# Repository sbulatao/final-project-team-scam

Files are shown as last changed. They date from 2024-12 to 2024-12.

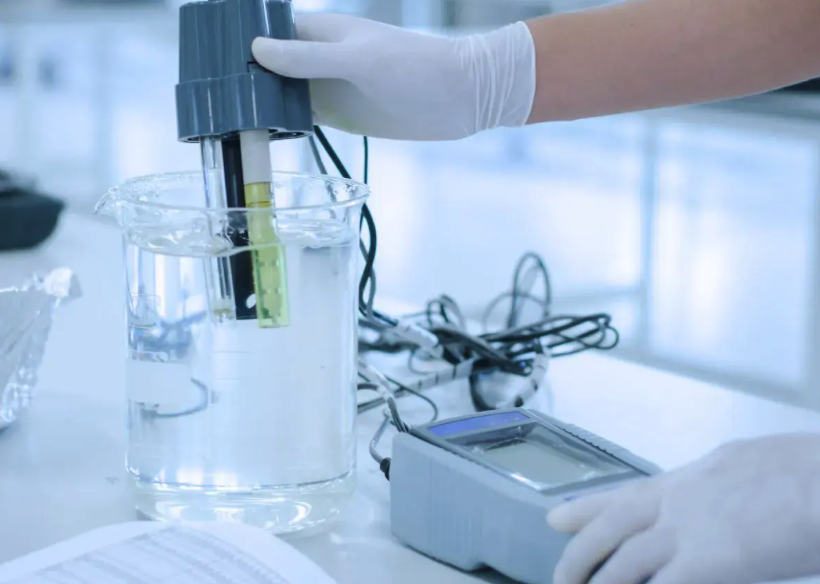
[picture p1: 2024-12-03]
pictures/testingIsh.png

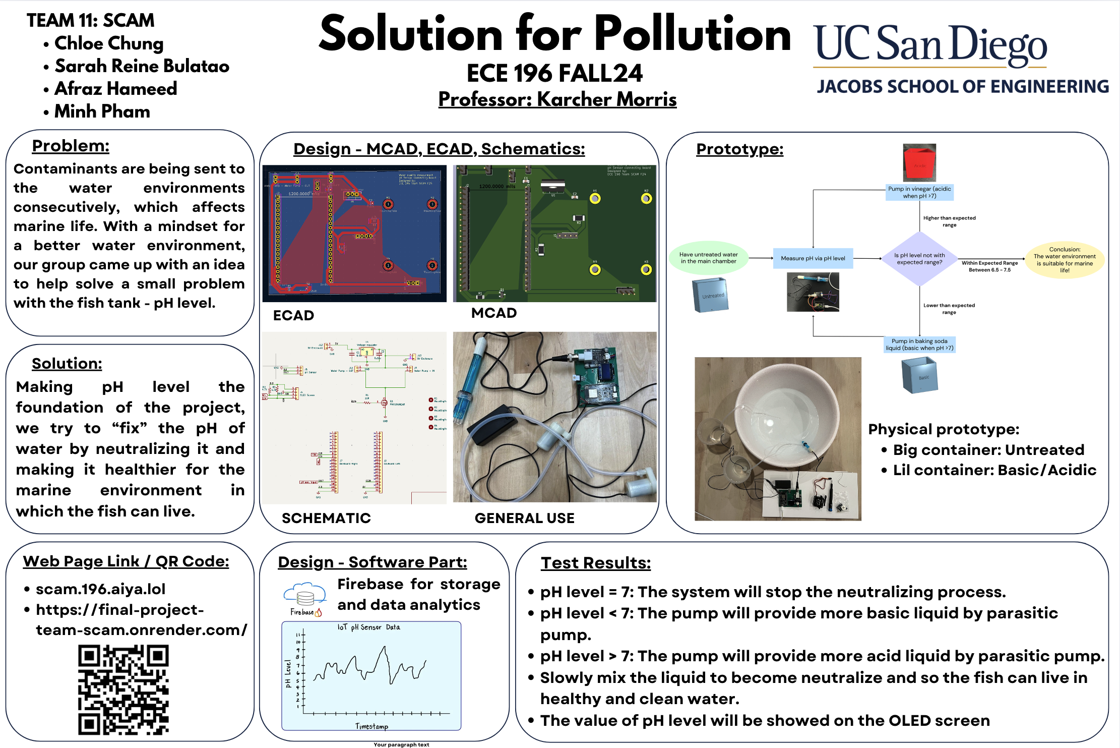
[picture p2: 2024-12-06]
pictures/canvaPoster.png

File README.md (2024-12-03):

# SolutionForpollution
GitHub Repo for ECE 196 Project Managing code, PCB files, 3D design, and more.

## WEBSITES: 
https://scam.196.aiya.lol/

https://final-project-team-scam.onrender.com

## Structure:
- css file contains all the css: the style for the website

- pictures file contains all the pictures: jpeg, png, etc.

- public file contains all the js: the action-ish for the website

- views file contains all the html: the bone structure for the website

## PROBLEM DEFINTION
Stormwater and Sewage Spills contain untreated debris directly into the Tijuana River and Imperial Beach affecting pH of the waters affecting marine life and making it more acidic.

## PROPOSED IDEA
A Real-Time Water pH Regulation Network

 - Big idea is pumping in basic solution in untreated water to regulate pH for marine life
 - Starting with pH sensor to determine levels, and pumping basic solution until it’s a regular level

## TESTABLE HYPOTHESIS
If there is polluted water with a more acidic pH, then our device will read the values and add basic solution until the pH is regular/safe for marine life.

## MILESTONES / TIMELINE
1. Completed PCB design on KiCAD and received parts from shipping
2. Assembled PCB with all necessary SMD’s and components and verified successful communication with computer (the device is recognized)
3. Finished 3D printing for basic solution enclosure, path for tube, body for contaminated water and measurement, and plastic cup to gather and pour water (not 3D printed)
4. Completed code for pH sensor data collection and logging to read and display pH values over time for both regular and contaminated water, with pH data collected and tabulated
5. Finished code and hardware integration for pumping with connections to PCB and recognizing pump in Arduino, basic solution can travel in pump to water and stop pumping when correct pH is read. 
6. Testing and data collection in Untreated Water, testing out conditions for demo by recording video of shown, unclean dirty water with higher pH levels and showing pumping solution regulating pH levels until level is sustainable for marine life.

## References, Citations, Helpful Resources

# HTML References
FreeFrontend. 2016-2024. https://freefrontend.com/css-water-effects/

HTML5UP. https://html5up.net/ (Didn't Use but thinking about it)

## Research / Arduino Build

Fahad, Engr. Electronic Clinic. 8 March 2020. IOT Water Quality Monitoring Using Arduino, pH Sensor, Nodemcu ESP8266. https://www.electroniclinic.com/iot-water-quality-monitoring-using-arduinoph-sensornodemcu-esp8266/

Ani, Emmanuel. hackster.io. 4 May 2024. Water Quality Monitoring and Notification System. https://www.hackster.io/eani/water-quality-monitoring-and-notification-system-f85d23 

YSI: a company that works on the water quality measurement which is The Sydney Institute of Marine Science collaborative
https://www.ysi.com/

United States Environmental Protection Agency. 21 October 2024. Water Quality Standards: Regulations and Resources. https://www.epa.gov/wqs-tech

Standard Methods For the Examination of Water and Wastewater. https://www.standardmethods.org

https://www.nsf.org/nsf-standards/standards-portfolio/water-wastewater-standards

(ERROR 404 GIVEN) https://www.nsf.org/our-services/water-quality

(ERROR 404 GIVEN) https://www.instructables.com/howto/water+quality+monitor/

## Website for the San Diego Coast Keepers EVIDENCE:

- Home page. https://www.sdcoastkeeper.org/
- Stormwater Infrastructure. https://www.sdcoastkeeper.org/water-quality/stormwater-infrastructure-funding/
- Tijuana River Sewage Crisis. https://www.sdcoastkeeper.org/tijuana-river-sewage/

## Other EVIDENCE:

Museg, Phillip. San Diego CoastKeeper. 2 May 2024. Understanding The Tijuana River Sewage Crisis - An Overview of Causes and Consequences. https://www.sdcoastkeeper.org/blog/tijuana-river-sewage-crisis-causes-consequences/

The California Water Boards. 25 September 2024. USIBWC Spill Events and Transboundary Flow Events from Mexico into the San Diego Region. https://www.waterboards.ca.gov/sandiego/water_issues/programs/tijuana_river_valley_strategy/sewage_issue.html

SDSU News Team. 14 February 2024. New Report: Public Health Crisis Unfolds as Tijuana River Sewage Contamination Escalates. https://www.sdsu.edu/news/2024/02/public-health-crisis-unfolds-as-tijuana-river-sewage-contamination-escalates

Shin, Tony. Fox 5 Kusi News. 11 September 2024. Imperial Beach Sewage Crisis Causing Fears of Long-Term Illnesses. https://fox5sandiego.com/news/local-news/imperial-beach-sewage-crisis-causing-fears-of-long-term-illnesses/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,closed%20for%20over%201%2C000%20days.

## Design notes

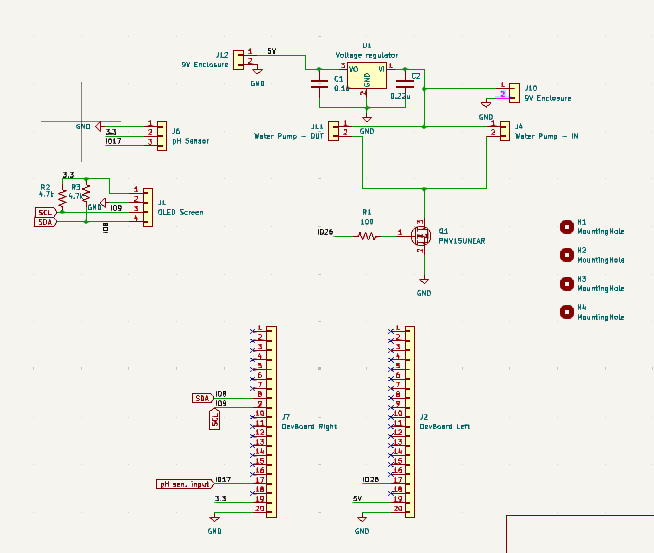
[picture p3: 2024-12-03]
pictures/Schematic.PNG

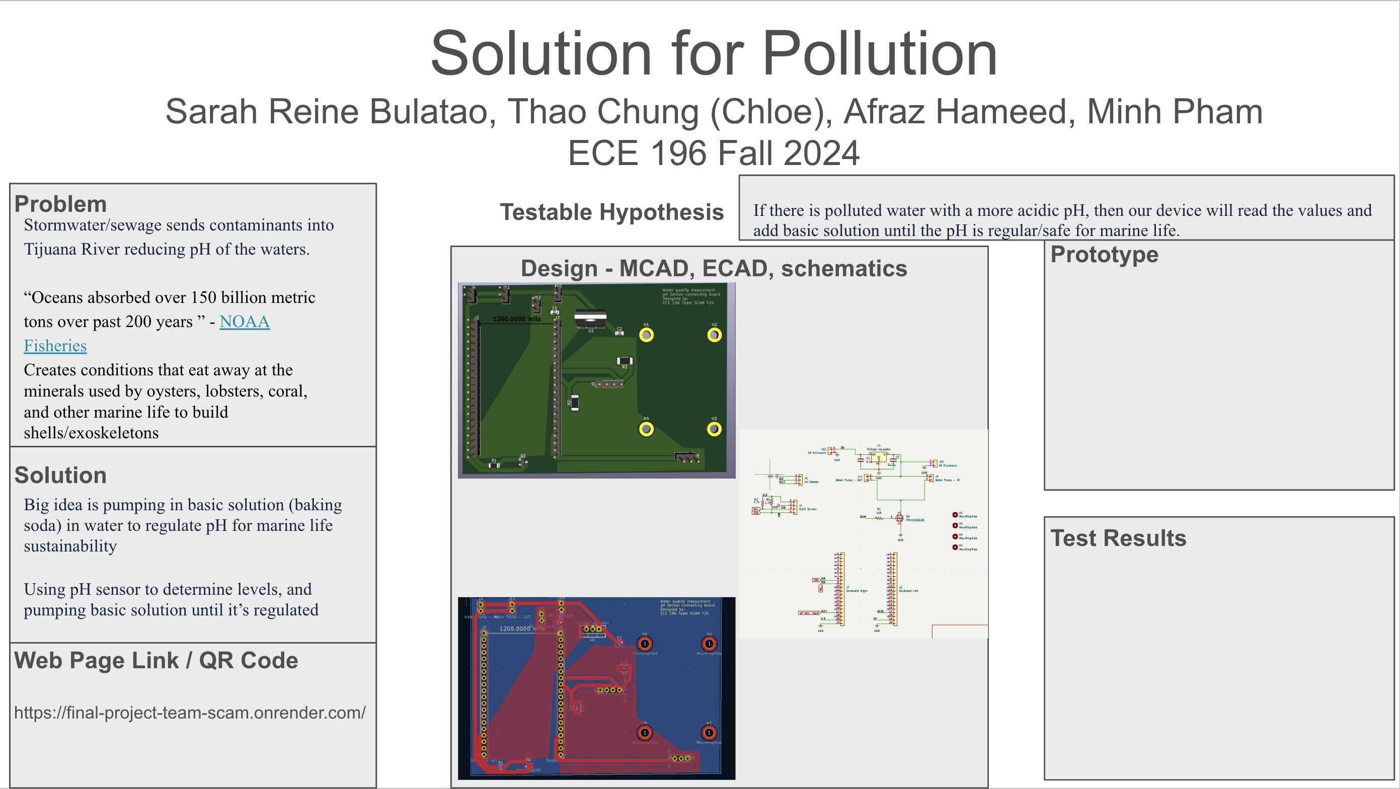
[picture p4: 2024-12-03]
pictures/poster.png

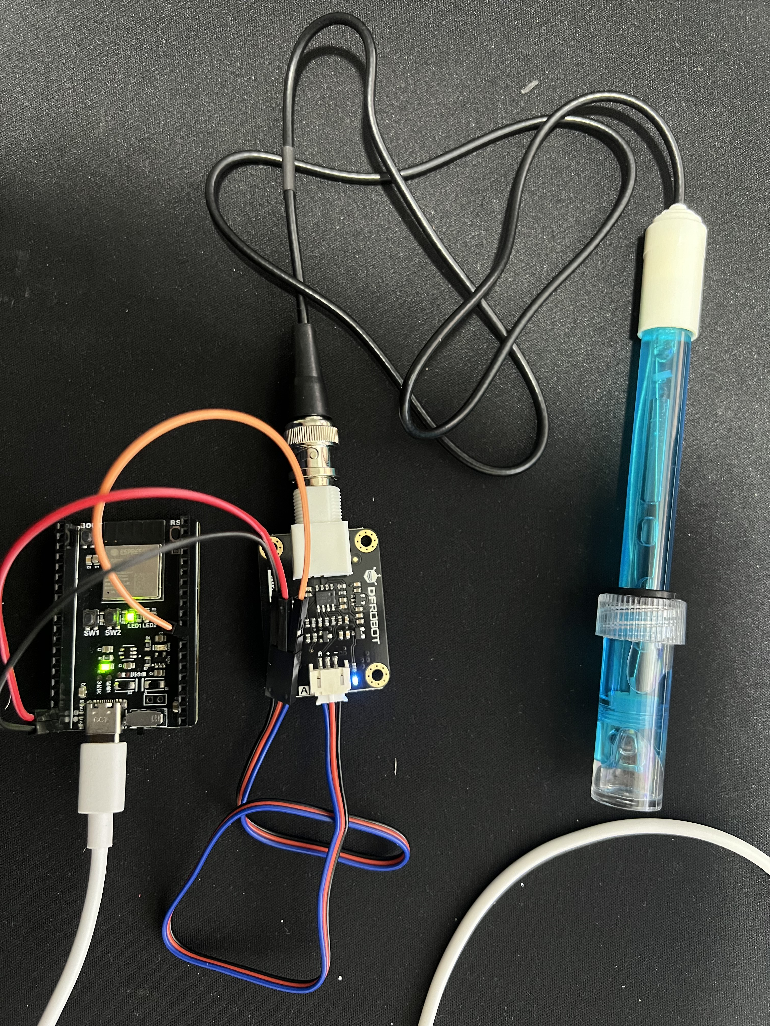
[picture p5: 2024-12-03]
pictures/pH_Sensor connected with ESP32S3.jpg

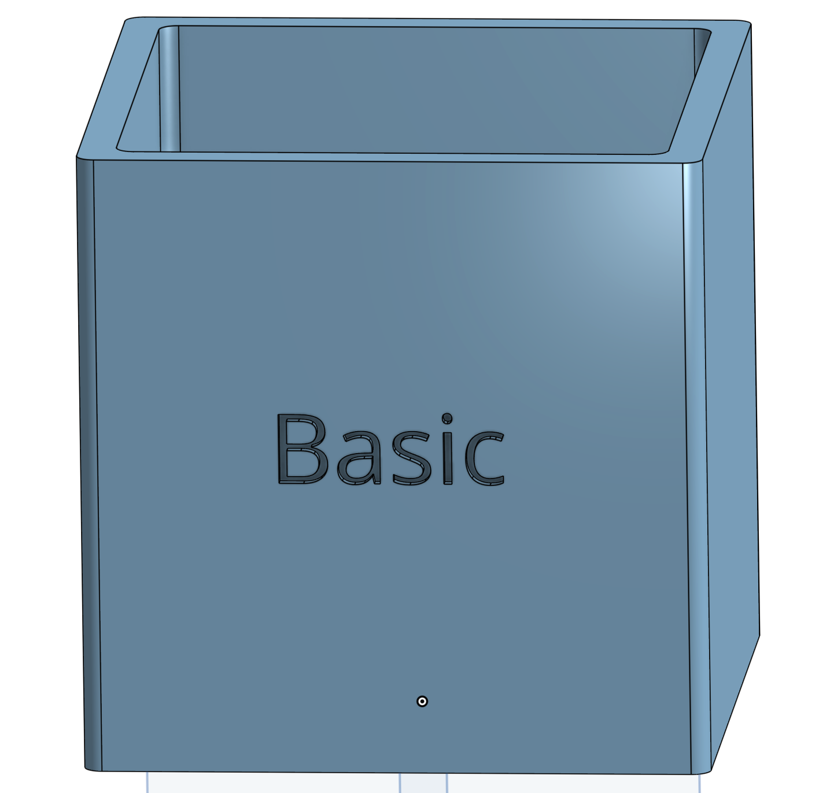
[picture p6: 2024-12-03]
pictures/CAD_basic.png

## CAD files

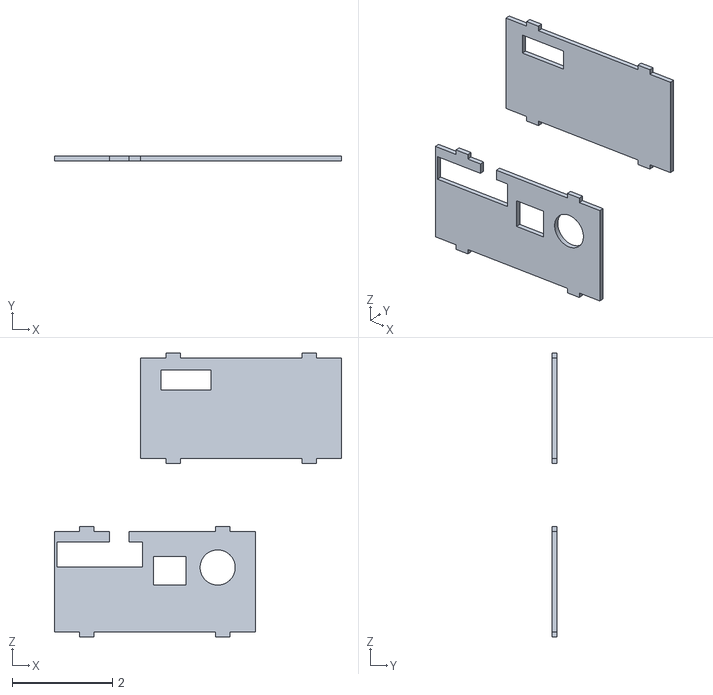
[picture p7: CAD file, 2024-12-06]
Enclosure/Top - Bottom PCB.stl
5.72 x 0.1 x 5.65

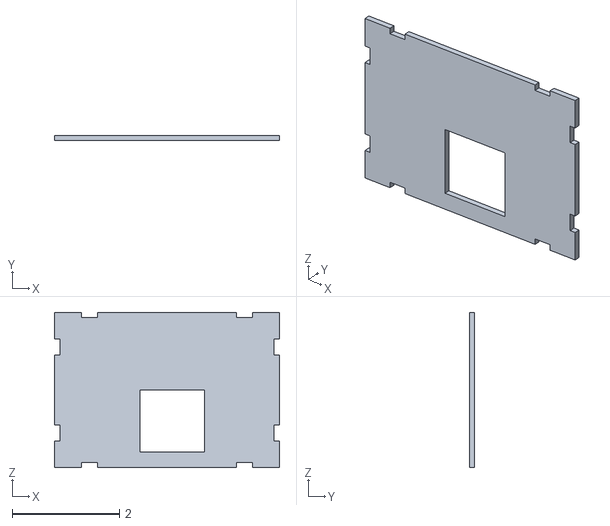
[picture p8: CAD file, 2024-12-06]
Enclosure/Top PCB.stl
4.20 x 0.1 x 2.90

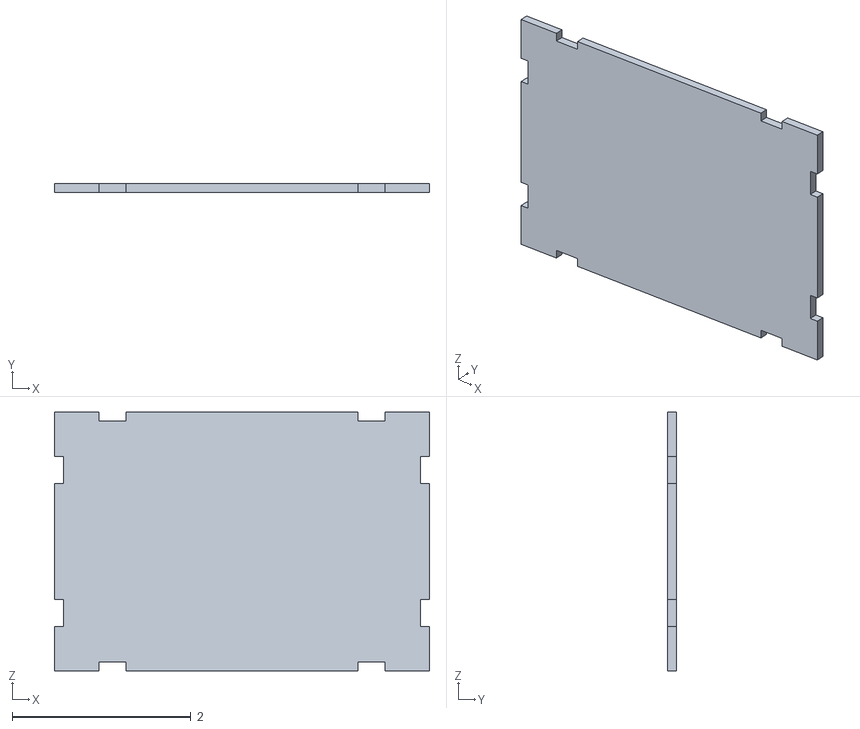
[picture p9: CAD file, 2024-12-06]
Enclosure/Bottom PCB.stl
4.20 x 0.1 x 2.90

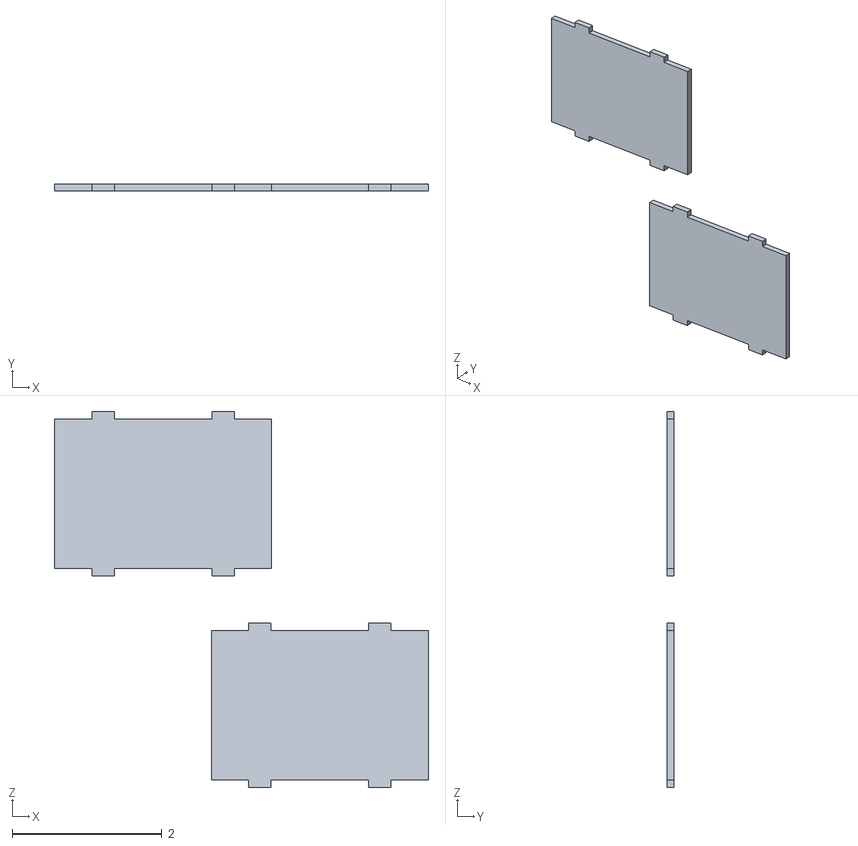
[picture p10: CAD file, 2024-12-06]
Enclosure/Left- Right PCB.stl
4.99 x 0.1 x 5.02

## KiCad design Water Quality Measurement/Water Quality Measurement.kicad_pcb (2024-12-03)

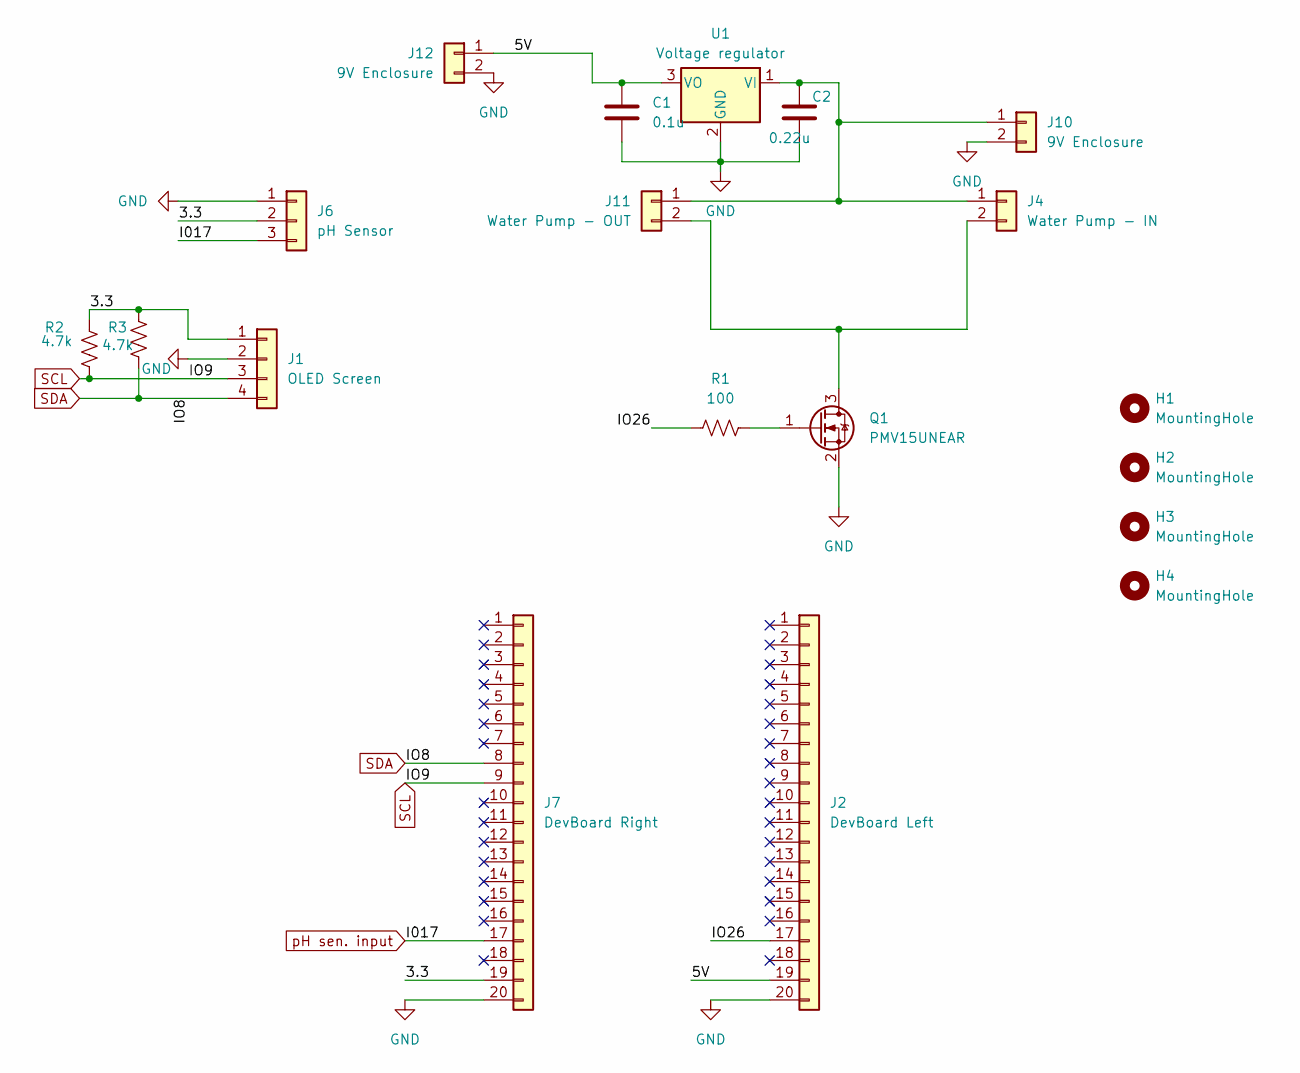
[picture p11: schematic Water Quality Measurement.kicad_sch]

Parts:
C1: 0.1u; C_0805_2012Metric_Pad1.18x1.45mm_HandSolder
C2: 0.22u; C_0805_2012Metric_Pad1.18x1.45mm_HandSolder
H1, H2, H3, H4: MountingHole; MountingHole_3.2mm_M3_ISO7380_Pad_TopBottom
J1: OLED Screen; PinHeader_1x04_P2.54mm_Vertical
J2: DevBoard Left; PinHeader_1x20_P2.54mm_Vertical
J4: Water Pump - IN; PinHeader_1x02_P2.54mm_Vertical
J6: pH Sensor; PinHeader_1x03_P2.54mm_Vertical
J7: DevBoard Right; PinHeader_1x20_P2.54mm_Vertical
J10, J12: 9V Enclosure; PinHeader_1x02_P2.54mm_Vertical
J11: Water Pump - OUT; PinHeader_1x02_P2.54mm_Vertical
Q1: PMV15UNEAR; SOT-23
R1: 100; R_1206_3216Metric
R2, R3: 4.7k; R_2010_5025Metric
U1: Voltage regulator; TO-220-3_Vertical

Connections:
/3.3: J1.1, J6.2, J7.19, R2.2, R3.2
/5V: C1.1, J2.19, J12.1, U1.3 (VO)
/IO26: J2.17, R1.1
GND: C1.2, C2.2, J1.2, J2.20, J6.1, J7.20, J10.2, J12.2, Q1.2 (S), U1.2 (GND)
unnamed: C2.1, J4.1, J10.1, J11.1, U1.1 (VI)
unnamed: J4.2, J11.2, Q1.3 (D)
unnamed: Q1.1 (G), R1.2
SCL: J1.3, J7.9, R2.1
SDA: J1.4, J7.8, R3.1
pH sen. input: J6.3, J7.17

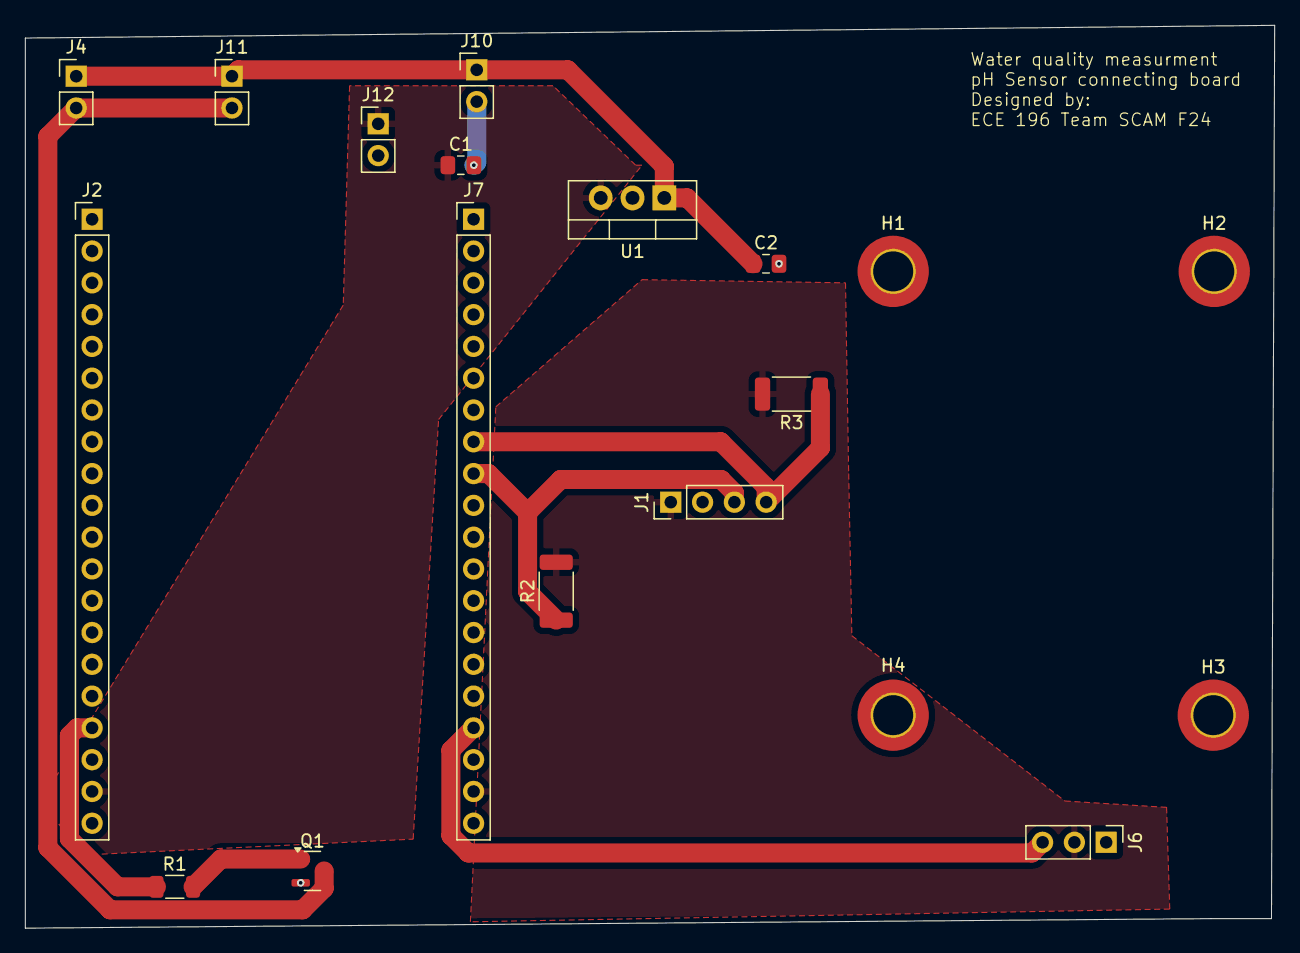
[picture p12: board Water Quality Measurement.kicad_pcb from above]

Board: 2 copper layers, 99.8 x 72.1 mm, 19 parts (0 on the bottom side), 10 nets.

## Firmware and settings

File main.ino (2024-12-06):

// #include "DFRobot_PH.h"
// #include <EEPROM.h>
#include <Wire.h>
#include <Adafruit_GFX.h>
#include <Adafruit_SSD1306.h>
#include <ESP32Servo.h> // make a class XD and analog write
// #include <Firebase_ESP_Client.h>
#include <FirebaseESP32.h>
#include <WiFi.h>
#include <HTTPClient.h>
#include <ArduinoJson.h>
// #include <time.h>

// Wi-Fi Configuration
// school
// #define WIFI_SSID "UCSD-PROTECTED"
// #define WIFI_USERNAME "sbulatao" 
// #define WIFI_PASSWORD "Bluemoon1sqxst*"
// #define NON_ENTERPRISE_WIFI_PASSWORD ""
// #define UCSD_PID "A17239438"
// home
#define WIFI_SSID "NETGEAR68"
#define WIFI_PASSWORD "melodicbird404"

// Firebase Configuration
#define FIREBASE_HOST "https://ece-196scamproject-default-rtdb.firebaseio.com/"
#define FIREBASE_AUTH "VqdCfSFN2HIRhih1ZGz8stDUESx4bc7i3w6MNGMB"

// Server Configuration
#define SERVER_URL "http://localhost:6543/pHSensorData/plot"

// OLED Configuration
#define SCREEN_WIDTH 128
#define SCREEN_HEIGHT 64
#define OLED_RESET -1
Adafruit_SSD1306 display(SCREEN_WIDTH, SCREEN_HEIGHT, &Wire, OLED_RESET);

// Pin Definitions
#define OLED_SCL 38
#define OLED_SDA 39
#define PH_SENSOR_PIN 16
#define PUMP_PIN 17
#define SERVO_PIN 15

// Global Variables
FirebaseData fbdo;
FirebaseAuth auth;
FirebaseConfig config;
float temperature = 25.0;  // Fixed temperature for simplicity
// DFRobot_PH phSensor;       // pH Sensor instance
Servo myServo;             // Servo instance
unsigned long lastSendTime = 0;

void connectToWiFi() {
    // Serial.print("Connecting to Wi-Fi");
    // WiFi.begin(WIFI_SSID, WIFI_USERNAME, WIFI_PASSWORD); // school
    WiFi.begin(WIFI_SSID, WIFI_PASSWORD); // home
    while (WiFi.status() != WL_CONNECTED) {
        delay(500);
        // Serial.print(".");
    }
    Serial.println("\nConnected to Wi-Fi.");
    Serial.print("IP Address: ");
    Serial.println(WiFi.localIP());
}

void initializeFirebase() {
    config.host = FIREBASE_HOST;
    config.signer.tokens.legacy_token = FIREBASE_AUTH;

    Firebase.begin(&config, &auth);
    Firebase.reconnectWiFi(true);

    if (Firebase.ready()) {
        Serial.println("Firebase initialized successfully!");
    } else {
        Serial.println("Failed to initialize Firebase.");
    }
}

String getFormattedTime() {
    time_t now = time(nullptr);
    struct tm* timeinfo = localtime(&now);
    char buffer[20];
    strftime(buffer, sizeof(buffer), "%Y-%m-%d %H:%M:%S", timeinfo);
    return String(buffer);
}


void sendDataToFirebase(float pH, String timestamp) {
    String counterPath = "/pHSensors/entryCount"; // Path to store the counter
    String entryPath;

    // Retrieve the current entry count from Firebase
    int entryCount = 0;
    if (Firebase.getInt(fbdo, counterPath)) {
        entryCount = fbdo.intData();
        Serial.print("Current entry count: ");
        Serial.println(entryCount);
    } else {
        Serial.println("Failed to retrieve entry count. Initializing to 0.");
    }

    // Reset the counter to 1 if it exceeds 20
    if (entryCount >= 20) {
        entryCount = 0; // Reset the counter
    }

    // Increment the entry count
    entryCount++;
    entryPath = "/pHSensors/entry" + String(entryCount); // Path for the new entry

    // Create a JSON object for the new entry
    FirebaseJson json;
    json.add("timestamp", timestamp);
    json.add("pH", pH);

    // Overwrite the data at the calculated entry path
    if (Firebase.setJSON(fbdo, entryPath, json)) {
        Serial.print("Data successfully stored at ");
        Serial.println(entryPath);
    } else {
        Serial.print("Error storing data: ");
        Serial.println(fbdo.errorReason());
    }

    // Update the counter in Firebase
    if (Firebase.setInt(fbdo, counterPath, entryCount)) {
        Serial.println("Entry counter updated successfully.");
    } else {
        Serial.print("Failed to update entry counter: ");
        Serial.println(fbdo.errorReason());
    }
}



void sendDataToServer(float pH, String timestamp) {
    if (WiFi.status() == WL_CONNECTED) {
        HTTPClient http;

        // Prepare JSON payload
        StaticJsonDocument<200> jsonDoc;
        jsonDoc["timestamp"] = timestamp;
        jsonDoc["pH"] = pH;

        String jsonPayload;
        serializeJson(jsonDoc, jsonPayload);

        http.begin(SERVER_URL); // Specify the endpoint
        http.addHeader("Content-Type", "application/json"); // Set content type to JSON

        int httpResponseCode = http.POST(jsonPayload); // Send the request

        if (httpResponseCode > 0) {
            // Serial.print("Server Response: ");
            Serial.println(http.getString());
        } else {
            Serial.print("Error sending POST request: ");
            Serial.println(httpResponseCode);
        }

        http.end(); // Close connection
    } else {
        Serial.println("Wi-Fi Disconnected. Cannot send data.");
    }
}

void setup() {
    // Initialize Serial Monitor
    Serial.begin(115200);
    connectToWiFi();

    // Initialize Firebase
    initializeFirebase();

    // Initialize EEPROM for calibration data storage
    //EEPROM.begin(512);

    // Initialize pH Sensor
    // phSensor.begin();
    // Serial.println("pH Sensor initialized. Calibrate with known buffer solutions if needed.");

    // Initialize I2C for OLED
    Wire.begin(OLED_SDA, OLED_SCL);

    // Initialize OLED Display
    if (!display.begin(SSD1306_SWITCHCAPVCC, 0x3C)) {
        // Serial.println(F("OLED initialization failed!"));
        for (;;);  // Halt execution
    }
    display.clearDisplay();
    display.setTextSize(1);
    display.setTextColor(SSD1306_WHITE);
    display.setCursor(0, 0);
    // display.println(F("OLED Initialized"));
    display.display();

    // Configure ADC
    analogReadResolution(12);          // Set ADC resolution to 12 bits
    analogSetAttenuation(ADC_11db);    // Set attenuation for full input range (0-3.3V)

    // Initialize Pump
    pinMode(PUMP_PIN, OUTPUT);
    digitalWrite(PUMP_PIN, LOW);  // Ensure pump is OFF initially

    // Initialize Servo
    myServo.attach(SERVO_PIN);
    myServo.write(90); // Set servo to the neutral position (90 degrees)

    // Synchronize Time via NTP
    configTime(0, 0, "pool.ntp.org", "time.nist.gov");
    // Serial.println("Synchronizing time...");
    while (time(nullptr) < 1000) { // Wait until time is synchronized
        delay(500);
        // Serial.print(".");
    }
    // Serial.println(" Time synchronized.");
}

void loop() {
    // Read pH sensor data
    int pHValue = analogRead(PH_SENSOR_PIN);
    float voltage = pHValue * (5 / 4095.0); // Convert ADC value to voltage (3.3V reference)
    float pH = 9 + ((2.5 - voltage) / 0.18); // Calculate pH value

    // Print results to Serial Monitor
    Serial.print("Raw ADC Value: ");
    Serial.print(pHValue);
    Serial.print(" | Voltage: ");
    Serial.print(voltage, 2);
    Serial.print("V | pH: ");
    Serial.println(pH);

    // Display pH on OLED
    display.clearDisplay();
    display.setCursor(0, 0);
    display.println(F("pH Sensor Reading:"));
    display.print(F("pH: "));
    display.println(pH, 2);
    // display.display();

    // Send data to Firebase and the server every 5 seconds
    if (millis() - lastSendTime > 5000) {
        lastSendTime = millis();
        String timestamp = getFormattedTime();
        sendDataToFirebase(pH, timestamp);
        // sendDataToServer(pH, timestamp);
    }

    String pumpStatus;
    String servoStatus;

  // Pump and Servo Control
  if (pH < 6.5 || pH > 8) {
    Serial.println("pH is out of range.");
    // Serial.println("Activating pump and moving servo...");
    digitalWrite(PUMP_PIN, HIGH);   // Turn on pump
    pumpStatus = "ON";
    servoStatus = "MOVING";
    // Oscillate the servo between 0° and 180°
    for (int angle = 0; angle <= 180; angle += 10) {
      myServo.write(angle);
      delay(100);  // Adjust speed of movement HERE
    }
    for (int angle = 180; angle >= 0; angle -= 10) {
      myServo.write(angle);
      delay(100);  // Adjust speed of movement HERE
    }
  } else {
    Serial.println("pH is within range.");
    // Serial.println("Turning off pump and resetting servo...");
    digitalWrite(PUMP_PIN, LOW);// Turn off pump
    pumpStatus = "OFF";
    servoStatus = "STOPPED";
    myServo.write(0); // Reset servo
  }
  // Display pump and servo status
  display.setCursor(0,20);
  display.print(F("Pump: "));
  display.println(pumpStatus);
  display.print(F("Servo: "));
  display.print(servoStatus);
  display.display();

  // Calibration (Optional, only when calibrating with buffer solutions)
  // phSensor.calibration(voltage, temperature);  // Uncomment this line for calibration

  delay(1000); // Delay before next reading
}

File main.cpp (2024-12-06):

#include <WiFi.h>
#include <FirebaseESP32.h>
#include "config.h"

// Firebase and WiFi objects
FirebaseData firebaseData;

void setup() {
  Serial.begin(115200);

#ifdef LOCATION_SCHOOL
  WiFi.begin(WIFI_SSID, WIFI_USERNAME, WIFI_PASSWORD);
#else
  WiFi.begin(WIFI_SSID, WIFI_PASSWORD);
#endif

  // Connect to WiFi
  Serial.print("Connecting to Wi-Fi");
  while (WiFi.status() != WL_CONNECTED) {
    delay(500);
    Serial.print(".");
  }
  Serial.println("\nConnected to Wi-Fi");

  // Initialize Firebase
  Firebase.begin(FIREBASE_HOST, FIREBASE_AUTH);
  Firebase.reconnectWiFi(true);

  // Test Firebase connection
  if (Firebase.setString(firebaseData, "/test/message", "ESP32 connected!")) {
    Serial.println("Firebase connected successfully!");
  } else {
    Serial.println("Firebase connection failed: " + firebaseData.errorReason());
  }
}

void loop() {
  // Simulate pH sensor data
  float phValue = random(60, 80) / 10.0;  // Random value between 6.0 and 8.0
  String timestamp = String(millis() / 1000);  // Use timestamp as seconds since boot

  // Push data to Firebase
  if (Firebase.pushJSON(firebaseData, "/pHSensors", "{\"timestamp\":\"" + timestamp + "\",\"value\":" + String(phValue) + "}")) {
    Serial.println("Data pushed successfully:");
    Serial.println("Timestamp: " + timestamp);
    Serial.println("Value: " + String(phValue));
  } else {
    Serial.println("Failed to push data: " + firebaseData.errorReason());
  }

  delay(5000);  // Send data every 5 seconds
}

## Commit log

2024-10-29 Repo Copy
    Copied items from private repo to official one
    [Solution PCB.kicad_pcb, Solution PCB.kicad_sch]
2024-10-29 Removed unnecessary files
    [Solution PCB.kicad_pcb, Solution PCB.kicad_sch]
2024-10-30 moved schematic/pcb circuit/3D view to pictures file
2024-10-31 added schematic pictures in schematic section
2024-10-31 fixed schematic layout
2024-11-14 added layout code for water pump
2024-11-23 added .cpp for esp32 for pHSensor values - in progress
2024-12-03 added pump status & servo status
2024-12-07 Added more text describing PCB and resources
2024-12-07 Updated PCB description again
2024-12-07 Final committs for updating schematics with annotations
2024-12-07 Enclosure update
    Put in picture for enclosure
